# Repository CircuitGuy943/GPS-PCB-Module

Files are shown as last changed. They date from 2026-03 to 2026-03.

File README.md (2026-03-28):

# GPS-PCB-Module
I needed a simple, but effective GPS capable PCB to accompany my Flight Controller on my drone and I decided to use the large flat area on top to utilise as much ground area as I could, because more ground area means better reception. So I made this PCB which maximises that area and provides me with an FPC connector which I can then attach to the main FC PCB and so use the GPS functionality.

## Features:
- Powerful L80RE-M37 GPS module combined with a ginormous ground plane for good reception.
- CR2032 cell battery holder for keeping time and reducing setup configuration needed
- 6-pin FPC carrying 3.3V power and UART connection to the MCU (not on this board)

## PCB
This is the PCB, simple double sided with cool silkscreen designs on top.

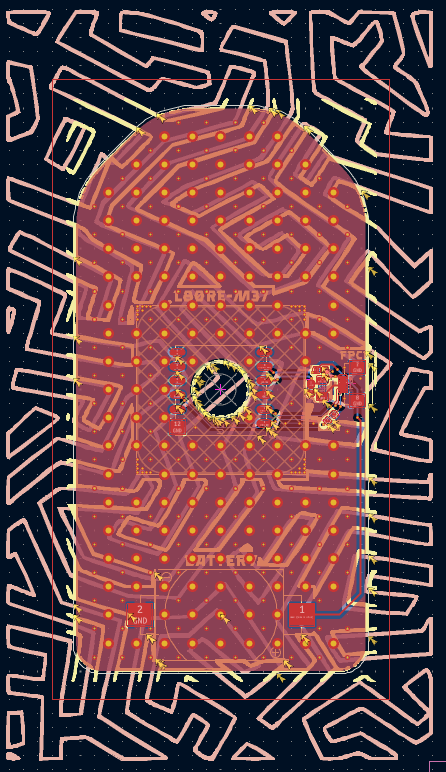
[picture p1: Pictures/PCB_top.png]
PCB Layer 1
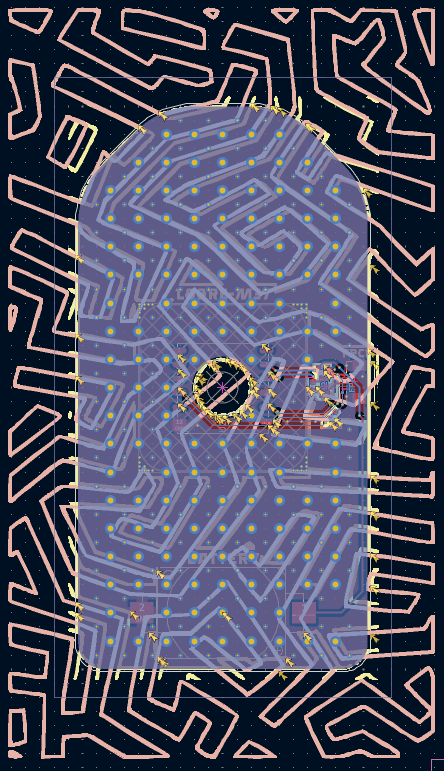
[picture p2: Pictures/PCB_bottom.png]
PCB Layer 2
 

## Schematic
And here is the schematic too:

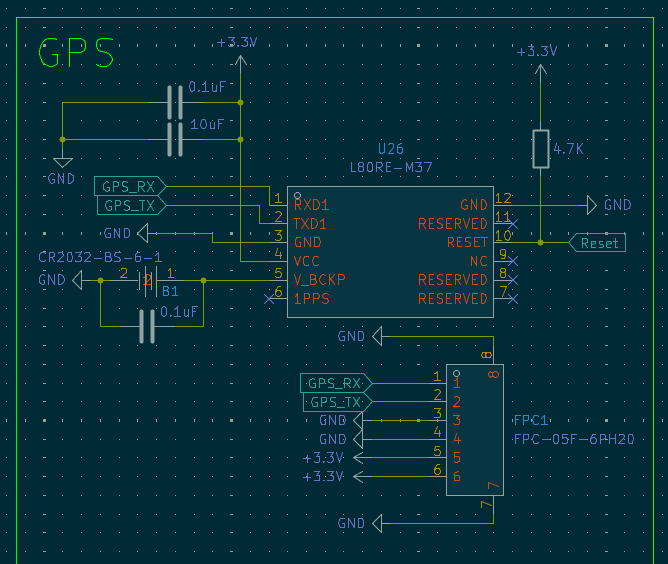
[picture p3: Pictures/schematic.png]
Schematic


## 3D renders
Here are also some 3D renders done in Fusion and KiCad to show off the PCB :)

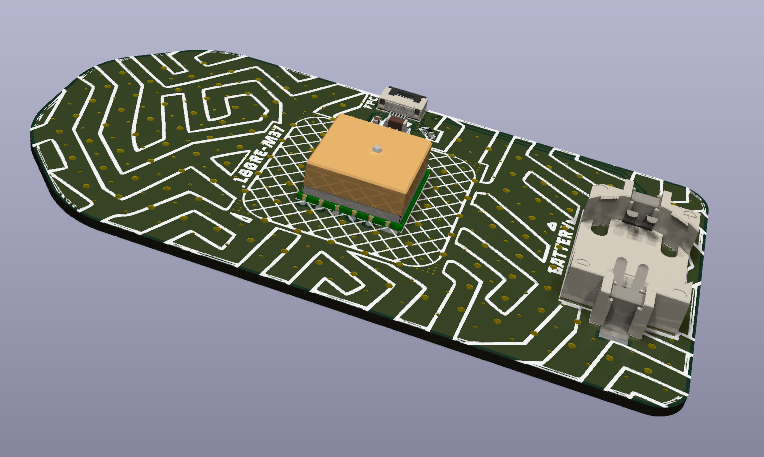
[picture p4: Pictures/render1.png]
Case render 1
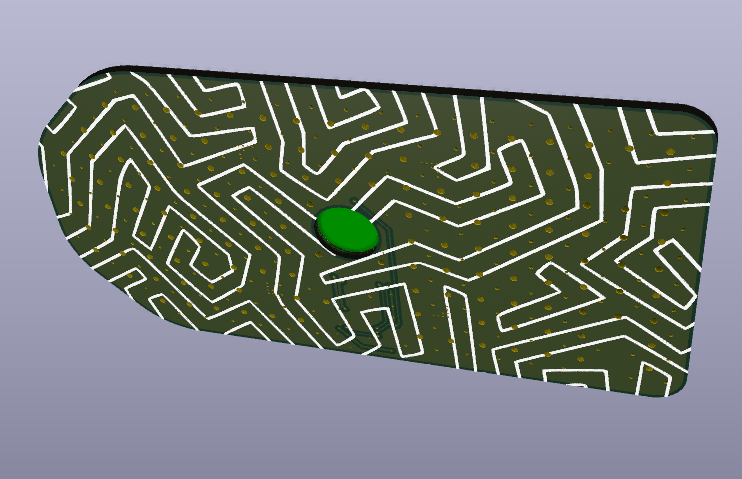
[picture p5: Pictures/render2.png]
Case render 2
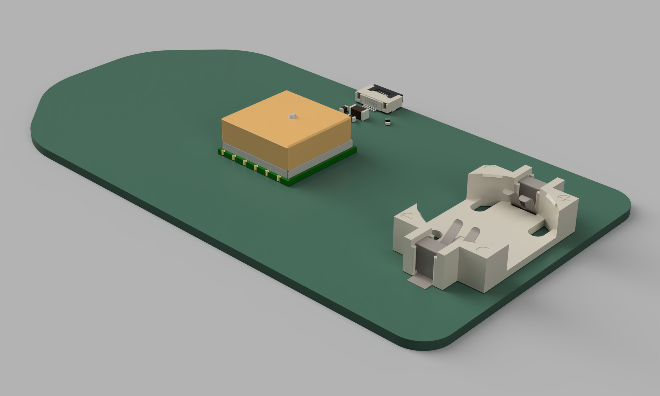
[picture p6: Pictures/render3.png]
Case render 3
   

## Firmware Overview
I've also included some basic firmware (**untested**) that should get the GPS module working with the UART connected to an MCU.

## BOM:
The BOM file with the prices is also found in the root directory.

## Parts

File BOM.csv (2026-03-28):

BOM
PCB | $5.57 | Basic PCB (Special Offer)
L80RE | $9.46 | Not availible on LCSC/JLCPCB | https://www.aliexpress.com/item/1005011635963638.html
LCSE parts | $12.52 | Cheaper than PCBA | https://www.lcsc.com/product-detail/C7498148.html
 |  |  | https://www.lcsc.com/product-detail/C14663.html
Total | $27.55 |  | https://www.lcsc.com/product-detail/C2856796.html
 |  |  | https://www.lcsc.com/product-detail/C13585.html
 |  |  | https://www.lcsc.com/product-detail/C23162.html

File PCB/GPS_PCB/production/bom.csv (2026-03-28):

Designator | Footprint | Quantity | Value | LCSC Part #
C120 | 1206 | 1 | 10uF
C79, C80 | 0603 | 2 | 0.1uF
FPC1 | FPC-SMD_6P-P0.50_XUNPU_FPC-05F-6PH20 | 1 | FPC-05F-6PH20 | C2856796
R1 | 0603 | 1 | 4.7K
U1 | BAT-TH_CR2032-BS-6-1 | 1 | CR2032-BS-6 | C22363833
U26 | GPSM-SMD_12P-L16.0-W16.0-P2.54-BL | 1 | L80RE-M37 | C3029061

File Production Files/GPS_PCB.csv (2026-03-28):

Id | Designator | Footprint | Quantity | Comment | Supplier and ref | Column1
1 | C80,C79 | C_0603_1608Metric | 2 | 0.1uF
2 | U26 | GPSM-SMD_12P-L16.0-W16.0-P2.54-BL | 1 | L80RE-M37
3 | R1 | R_0603_1608Metric | 1 | 4.7K
4 | FPC1 | FPC-SMD_6P-P0.50_XUNPU_FPC-05F-6PH20 | 1 | FPC-05F-6PH20
5 | C120 | C_1206_3216Metric | 1 | 10uF
6 | Battery | BAT-TH_CR2032-BS-6-1 | 1 | CR2032-BS-6-1

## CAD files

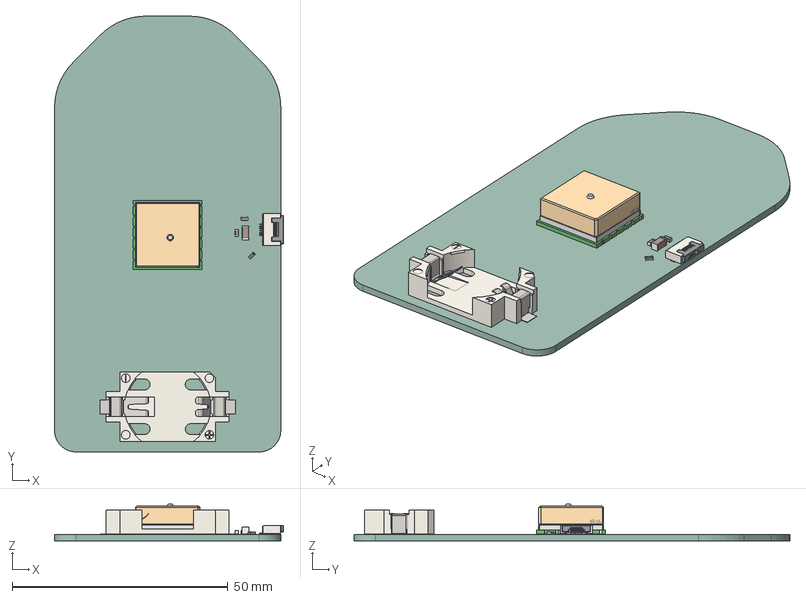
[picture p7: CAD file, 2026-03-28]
3D Models/GPS_PCB.step
53.0 x 100.9 x 8.54 mm
GPSM-SMD_12P-L16.0-W16.0-P2.54-BL
C_0603_1608Metric x 2
BAT-SMD_L28.5-W16.0-H5.5-LS31.3_CR2032-BS-6-1
C_1206_3216Metric
FPC-SMD_6P-P0.50_XUNPU_FPC-05F-6PH20
R_0603_1608Metric
GPS_PCB_PCB

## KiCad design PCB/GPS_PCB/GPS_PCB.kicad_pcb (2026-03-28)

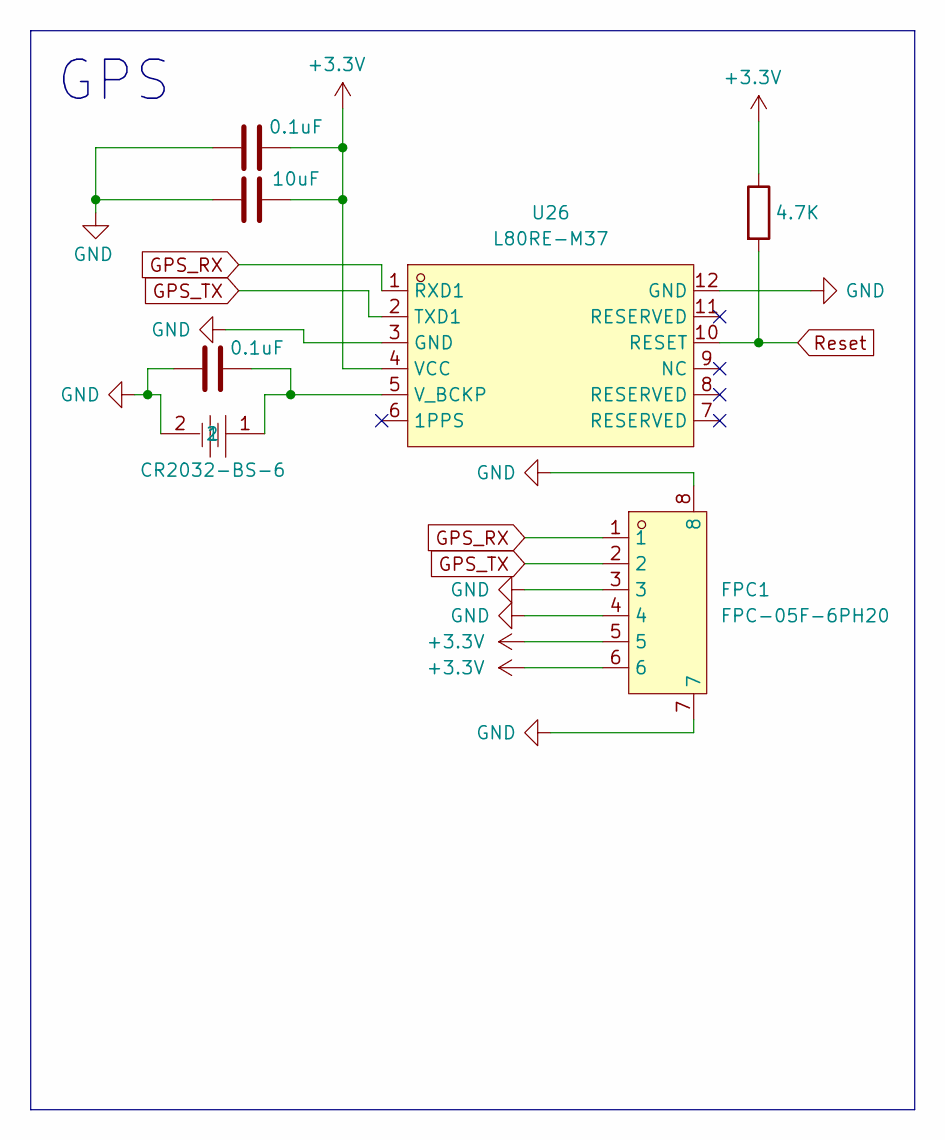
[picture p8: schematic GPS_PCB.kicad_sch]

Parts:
C79, C80: 0.1uF; C_0603_1608Metric
C120: 10uF; C_1206_3216Metric
FPC1: FPC-05F-6PH20; FPC-SMD_6P-P0.50_XUNPU_FPC-05F-6PH20; LCSC Part C2856796
R1: 4.7K; R_0603_1608Metric
U1: CR2032-BS-6; BAT-TH_CR2032-BS-6-1; LCSC Part C22363833
U26: L80RE-M37; GPSM-SMD_12P-L16.0-W16.0-P2.54-BL; LCSC Part C3029061

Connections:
+3.3V: C80.2, C120.2, FPC1.5, FPC1.6, R1.1, U26.4 (VCC)
GND: C79.1, C80.1, C120.1, FPC1.3, FPC1.4, FPC1.7, FPC1.8, U1.2, U26.3 (GND), U26.12 (GND)
GPS_RX: FPC1.1, U26.1 (RXD1)
GPS_TX: FPC1.2, U26.2 (TXD1)
unnamed: C79.2, U1.1, U26.5 (V_BCKP)
Reset: R1.2, U26.10 (RESET)

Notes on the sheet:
GPS

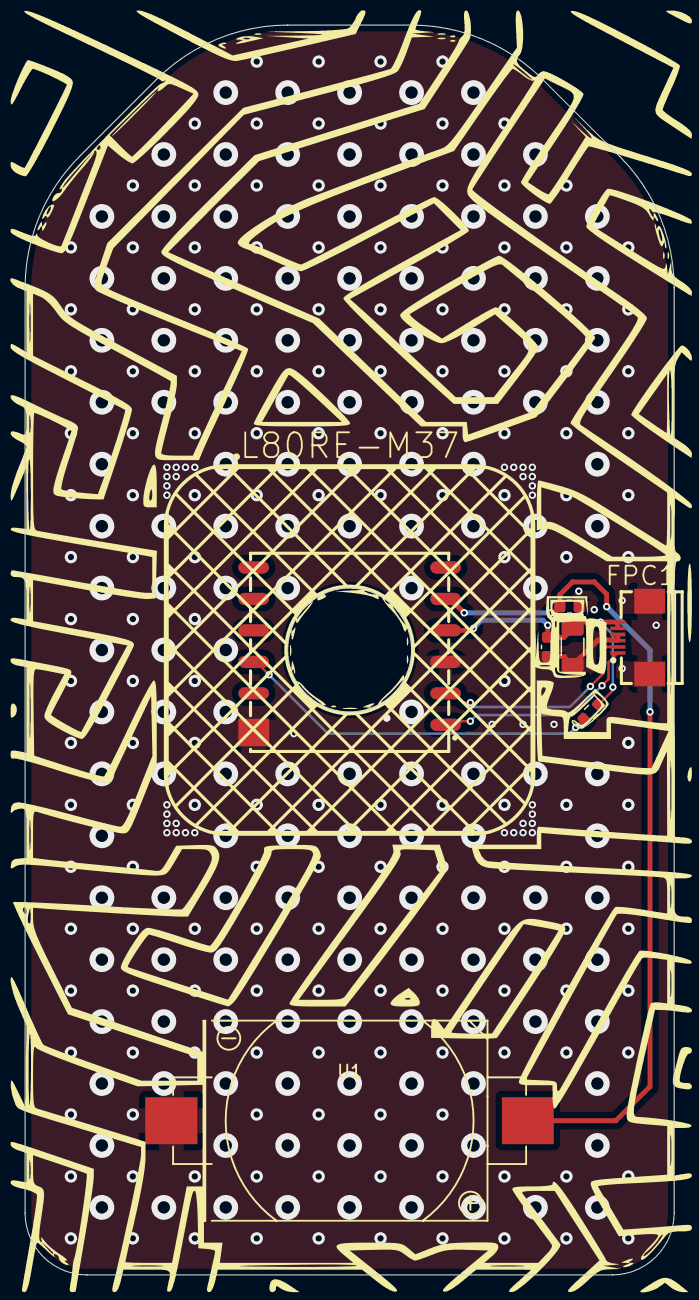
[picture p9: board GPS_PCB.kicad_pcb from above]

Board: 2 copper layers, 52.4 x 100.9 mm, 7 parts (0 on the bottom side), 6 nets.

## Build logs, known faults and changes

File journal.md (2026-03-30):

<!--
  This journal is auto generated by Hack Club Blueprint.
-->

# 3/25/2026 7:24 PM - Setup base for project, I will use the L80RE GPS Module  

_Time spent: 1.0h_  

(Working on my Flight controller project (for my drone) I realized I would want some GPS too, but that can't be mounted anywhere near the main electronics so instead I will mount the FC on the underside of the drone and mount the GPS PCB on the top, facing upwards, and since it's a completely separate PCB I will make it into a new project, simple but separate, so it's easier)

First off I found the L80RE-M37 and L96 GPS modules, the thing with the L96 module is it happens to have a much smaller antenna area, this would make reception much much weaker, whereas the L80 has a much bigger antenna so it makes my life easier. Adding more ground plane (which is the actual antenna for GPS apparently) would help even more. This is going to be a board that simply has a very large surface area with just the SMD GPS Module, a coin battery holder and maybe decoupling caps if needed. And an FPC connector so I can connect it to my main FC.



# 3/25/2026 7:48 PM - Made the schematic for the GPS module  

_Time spent: 1.5h_  

Simply followed the design guide https://www.dragino.com/downloads/downloads/datasheet/other_vendors/L80-R/Quectel_L80-R_Hardware_Design_V1.2.pdf, added a cell battery so that the time is kept even when the drone is turned off and disconnected from battery so that it doesn't have to be redone on every power up. And some necessary decoupling capacitors. Plus an FPC connector, the same connector will go on the flight controller, connected together by an FPC cable (I need to free some GPIO on the FC for UART, I didn't realize there'd be no I2C)



# 3/25/2026 9 PM - Made the PCB, positioned and routed.  

_Time spent: 2.0h_  

Positioned all the components, L80 in the center, the FPC on the right, and the cell battery at the bottom and also added the decoupling caps and stuff in the correct places. I also made sure to follow the design guide for the L80, and add the keep out area on the bottom of the board (I just made a hole in it) and the 30x30mm keep out zone. Added the few traces for the signal UART, power and the battery. The rest is just a massive ground plane with big vias to ensure a consistent plane and therefore good antenna and signal reception. Now I need to add a nice silkscreen mask, check DRC, put into fusion, take some renders then done. I don't need a case as this will just mount on top of my drone.



# 3/26/2026 7 PM - Added some vias and adjusted board.  

_Time spent: 0.7h_  

I had to change a few things after getting some help about the design of this, such as adding waaaaay more vias and running traces through vias on the bottom plane onto the underside of the module.



# 3/26/2026 8:17 PM - Added PCB artwork  

_Time spent: 1.5h_  

Added some really cool designs that I found using Inkscape to vectorize them from bitmaps to SVG files that I can then add as silkscreen covers. I also made sure to use masks to cover any components on the board so that the silkscreen didn't collide with them.






# 3/26/2026 8:47 PM - Checked DRC, tried putting into Fusion to make renders.  

_Time spent: 1.0h_  

I checked the DRC for the PCB and fixed most of the problems (traces too close, annular width etc) however there are a bunch of warnings but it's fine because these are just from the silkscreen clipping the board's edge but they'll get removed automatically so it's perfectly fine to have it like this.

I also tried exporting a STEP file of the board, however I only managed to export board only and components, if I tried exporting other stuff such as vias/traces/planes etc I get this weird error about the tolerance part (0.1/0.01/0.001 etc) of sizes being wrong, even though I've changed nothing in terms of that so I just left it as is and got a render of just the board with components and it should be fine, I did get some renders from KiCad's internal 3D viewer though.





# 3/28/2026 - Made some basic firmware.  

_Time spent: 1.0h_  

This is just some basic firmware to satisfy the requirement, the actual firmware running this will be on the flight controller. This mostly just sets up the UART connection and serial PC connection and gets GPS location data.



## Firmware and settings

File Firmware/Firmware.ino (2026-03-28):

#include <TinyGPS++.h>
#include <SoftwareSerial.h>

static const int RXPin = 4;
static const int TXPin = 3;
static const uint32_t GPSBaud = 9600;

TinyGPSPlus gps;
SoftwareSerial ss(RXPin, TXPin);

void setup() {
  Serial.begin(115200);
  Serial.println(F("L80‑RE‑M37 GPS Parser"));
  Serial.println(F("Initializing GPS module..."));
  ss.begin(GPSBaud);
  Serial.println(F("GPS serial started – waiting for fix..."));
}

void loop() {
  while (ss.available() > 0) {
    char c = ss.read();
    gps.encode(c);
  }

  if (gps.location.isValid()) {
    Serial.print(F("Latitude: "));
    Serial.print(gps.location.lat(), 6);
    Serial.print(F(" Longitude: "));
    Serial.print(gps.location.lng(), 6);

    if (gps.altitude.isValid()) {
      Serial.print(F(" Altitude: "));
      Serial.print(gps.altitude.meters());
      Serial.print(F(" m"));
    }

    if (gps.date.isValid()) {
      Serial.print(F(" Date: "));
      Serial.print(gps.date.month());
      Serial.print(F("/"));
      Serial.print(gps.date.day());
      Serial.print(F("/"));
      Serial.print(gps.date.year());
    }
    if (gps.time.isValid()) {
      Serial.print(F(" Time: "));
      if (gps.time.hour() < 10) Serial.print(F("0"));
      Serial.print(gps.time.hour());
      Serial.print(F(":"));
      if (gps.time.minute() < 10) Serial.print(F("0"));
      Serial.print(gps.time.minute());
      Serial.print(F(":"));
      if (gps.time.second() < 10) Serial.print(F("0"));
      Serial.print(gps.time.second());
    }

    if (gps.satellites.isValid()) {
      Serial.print(F(" Satellites: "));
      Serial.print(gps.satellites.value());
    }

    if (gps.hdop.isValid()) {
      Serial.print(F(" HDOP: "));
      Serial.print(gps.hdop.hdop());
    }

    Serial.println();
    delay(1000);
  } else {
    static unsigned long lastPrint = 0;
    if (millis() - lastPrint > 1000) {
      Serial.print(F("."));
      lastPrint = millis();
    }
  }
}

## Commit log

2026-03-08 Add main files
    [GPS_PCB.kicad_pcb, GPS_PCB.kicad_sch]
2026-03-28 Enhance README with detailed project information
    Expanded the README to include detailed features, PCB description, schematic, 3D renders, firmware overview, and BOM information.
